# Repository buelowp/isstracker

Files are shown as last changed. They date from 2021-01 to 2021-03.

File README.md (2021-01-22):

# Use an opaque globe to show the position of the ISS using a laser
This project is going to project the ISS location on a globe showing current position continuously. The system uses a Particle Argon, one stepper motor for longitude rotation, and one servo motor for latitude rotation. It also uses a LOT of other parts listed in the BOM to make this work.

The goal is to provide a good looking device that is accurate and consistent. All of the motors and electronics must be hidden, and all parts must be independently moveable. So, the globe must be able to rotate without changing where the laser is pointing. The laser must work inside the globe independent of the base. The laser must also rotate 360 degrees longitude. The ISS does not go above or below ~60 degrees latitude, so a simple servo can be used for that.

A Particle project named isstracker

I found a similar project using an ESP8266 about 5 years ago and I was intrigued. So, I started hacking something up, but my requirements became much more complex than the original project. I wanted full rotation and to be able to *spin* the globe sitting on a base without changing where the location of the point showing the ISS.

It uses two independent sliprings which provide the ability to rotate the globe and the armature holding the laser without losing precision. It uses one 200 step NEMA stepper for longitude, and one 160 degree servo for the latitiude. The laser is from Sparkfun, but any laser that can be powered by 3 volts would work.

Pictures to follow

## Building it

Instructions to follow

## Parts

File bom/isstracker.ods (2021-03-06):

Part | Value | Device | Package | Description | MF | MPN | PROD_ID | VALUE
C1 | 100uF | 100UF-POLAR-RADIAL-2.5MM-25V-20% | CPOL-RADIAL-2.5MM-6.5MM | 100µF polarized capacitors |  |  | CAP-08439 | 100uF
C2 | 100uF | 100UF-POLAR-RADIAL-2.5MM-25V-20% | CPOL-RADIAL-2.5MM-6.5MM | 100µF polarized capacitors |  |  | CAP-08439 | 100uF
D1 | 1N4004 | 1N4004 | DO41-10 | DIODE | On Semi
H1 | MOUNT-HOLE3.0 | MOUNT-HOLE3.0 | 3,0 | MOUNTING HOLE with drill center marker
H2 | MOUNT-HOLE3.0 | MOUNT-HOLE3.0 | 3,0 | MOUNTING HOLE with drill center marker
H3 | MOUNT-HOLE3.0 | MOUNT-HOLE3.0 | 3,0 | MOUNTING HOLE with drill center marker
H4 | MOUNT-HOLE3.0 | MOUNT-HOLE3.0 | 3,0 | MOUNTING HOLE with drill center marker
H6 | MOUNT-HOLE2.8 | MOUNT-HOLE2.8 | 2,8 | MOUNTING HOLE with drill center marker
IC2 | L7805CV | MC7805CT-BPMS-ND | TO220V | Positive VOLTAGE REGULATOR
J1 | MOTOR_RIGHT | CONN_16 | 1X16 | Feather Header | Adafruit | 2886
J2 | MOTOR | CONN_04 | 1X04 | Multi connection point. Often used as Generic Header-pin footprint for 0.1 inch spaced/style header connections |  |  | CONN-09696
J3 | MOTOR_LEFT | CONN_12 | 1X12 | Feather Header
J4 | DISPLAY | CONN_07 | 1X07 | Multi connection point. Often used as Generic Header-pin footprint for 0.1 inch spaced/style header connections | Adafruit | 2886
J5 | GLOBE_RESET | CONN_02 | 1X02 | Multi connection point. Often used as Generic Header-pin footprint for 0.1 inch spaced/style header connections
J6 | CONTROL | CONN_04 | 1X04 | Multi connection point. Often used as Generic Header-pin footprint for 0.1 inch spaced/style header connections |  |  | CONN-09696
J8 | UART | CONN_03 | 1X03 | Multi connection point. Often used as Generic Header-pin footprint for 0.1 inch spaced/style header connections
J9 | DISTANCE | CONN_03 | 1X03 | Multi connection point. Often used as Generic Header-pin footprint for 0.1 inch spaced/style header connections
LED1 | LEDCHIPLED_1206 | XZDG55W-3 | CHIPLED_1206 | green smd LED | SunLED | XZDG55W-3
LED3 | LEDCHIPLED_1206 | XZDG55W-3 | CHIPLED_1206 | green smd LED | SunLED | XZDG55W-3
Q2 | IRL3103PBF | IRL3103PBF | TO220V | N-channel MOSFETs | Infineon | IRL3103PBF
R1 | 1k | RCG08051K00JNEA | 0805 | 1k smd resistor | Vishay Dale | RCG08051K00JNEA | RES-11622 | 1k
R2 | 1k | RCG08051K00JNEA | 0805 | 1k smd resistor | Vishay Dale | RCG08051K00JNEA | RES-08474 | 1k
R3 | 100 | CRCW0805100RJNEAC‎ | 0805 | 100 ohm smd resistor | Vishay Dale | CRCW0805100RJNEAC‎ | RES-08474 | 100
R4 | 10k | CRCW080510K0FKTA | 0805 | 10k smd resistor | Vishay Dale | CRCW080510K0FKTA | RES-08474 | 10k
R5 | 10k | CRCW080510K0FKTA | 0805 | 10k smd resistor | Vishay Dale | CRCW080510K0FKTA | RES-08474 | 10k
U1 | ARGON | ARGON | Feather | ARGON | Particle
X1 | +12V | KK-156-2 | KK-156-2 | KK 156 HEADER | MOLEX

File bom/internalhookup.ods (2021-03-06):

Part | Value | Device | Package | Description | AVAILABILITY | DESCRIPTION | MF | MP | PACKAGE | PRICE | PROD_ID | VALUE
C1 | 100uF | 100UF-POLAR-RADIAL-2.5MM-25V-20% | CPOL-RADIAL-2.5MM-6.5MM | 100µF polarized capacitors |  |  |  |  |  |  | CAP-08439 | 100uF
C3 | 100uF | 100UF-POLAR-RADIAL-2.5MM-25V-20% | CPOL-RADIAL-2.5MM-6.5MM | 100µF polarized capacitors |  |  |  |  |  |  | CAP-08439 | 100uF
CN1 | LASER | JST_2PIN-THM-RA | JST-PH-2-THM-RA | JST 2-Pin Connectors of various flavors
J2 | SERVO | CONN_03 | 1X03 | Multi connection point. Often used as Generic Header-pin footprint for 0.1 inch spaced/style header connections
J3 | CONTROL | CONN_04 | 1X04 | Multi connection point. Often used as Generic Header-pin footprint for 0.1 inch spaced/style header connections |  |  |  |  |  |  | CONN-09696
J4 | AZIMUTH | CONN_03 | 1X03 | Multi connection point. Often used as Generic Header-pin footprint for 0.1 inch spaced/style header connections
Q2 | SMMBT2222ALT | MMBT3904 | SOT95P240X120-3N | MMBT3904 Series 40 V CE Breakdown 0.2 A NPN General Purpose Amplifier - SOT-23 Check prices | Bad | Bipolar (BJT) Transistor NPN 40V 200mA 300MHz 300mW Surface Mount SOT-23-3 | STMicroelectronics | MMBT3904 | SOT-23-3 Taiwan Semiconductor | None
R1 | 1k | RCG08051K00JNEA | 0805 | 1k ohm resistor |  |  |  |  |  |  | RES-11622 | 0.3
U1 | AMS1117-3.3 | AMS1117-3.3 | SOT229P700X180-4N | Sot223/Pkg 1-Amp 3.3-Volt Low Drop Out Voltage Regulatator | Unavailable | Sot223/Pkg 1-Amp 3.3-Volt Low Drop Out Voltage Regulatator | Advanced Monolithic Systems | AMS1117-3.3 | SOT-89 ams | None

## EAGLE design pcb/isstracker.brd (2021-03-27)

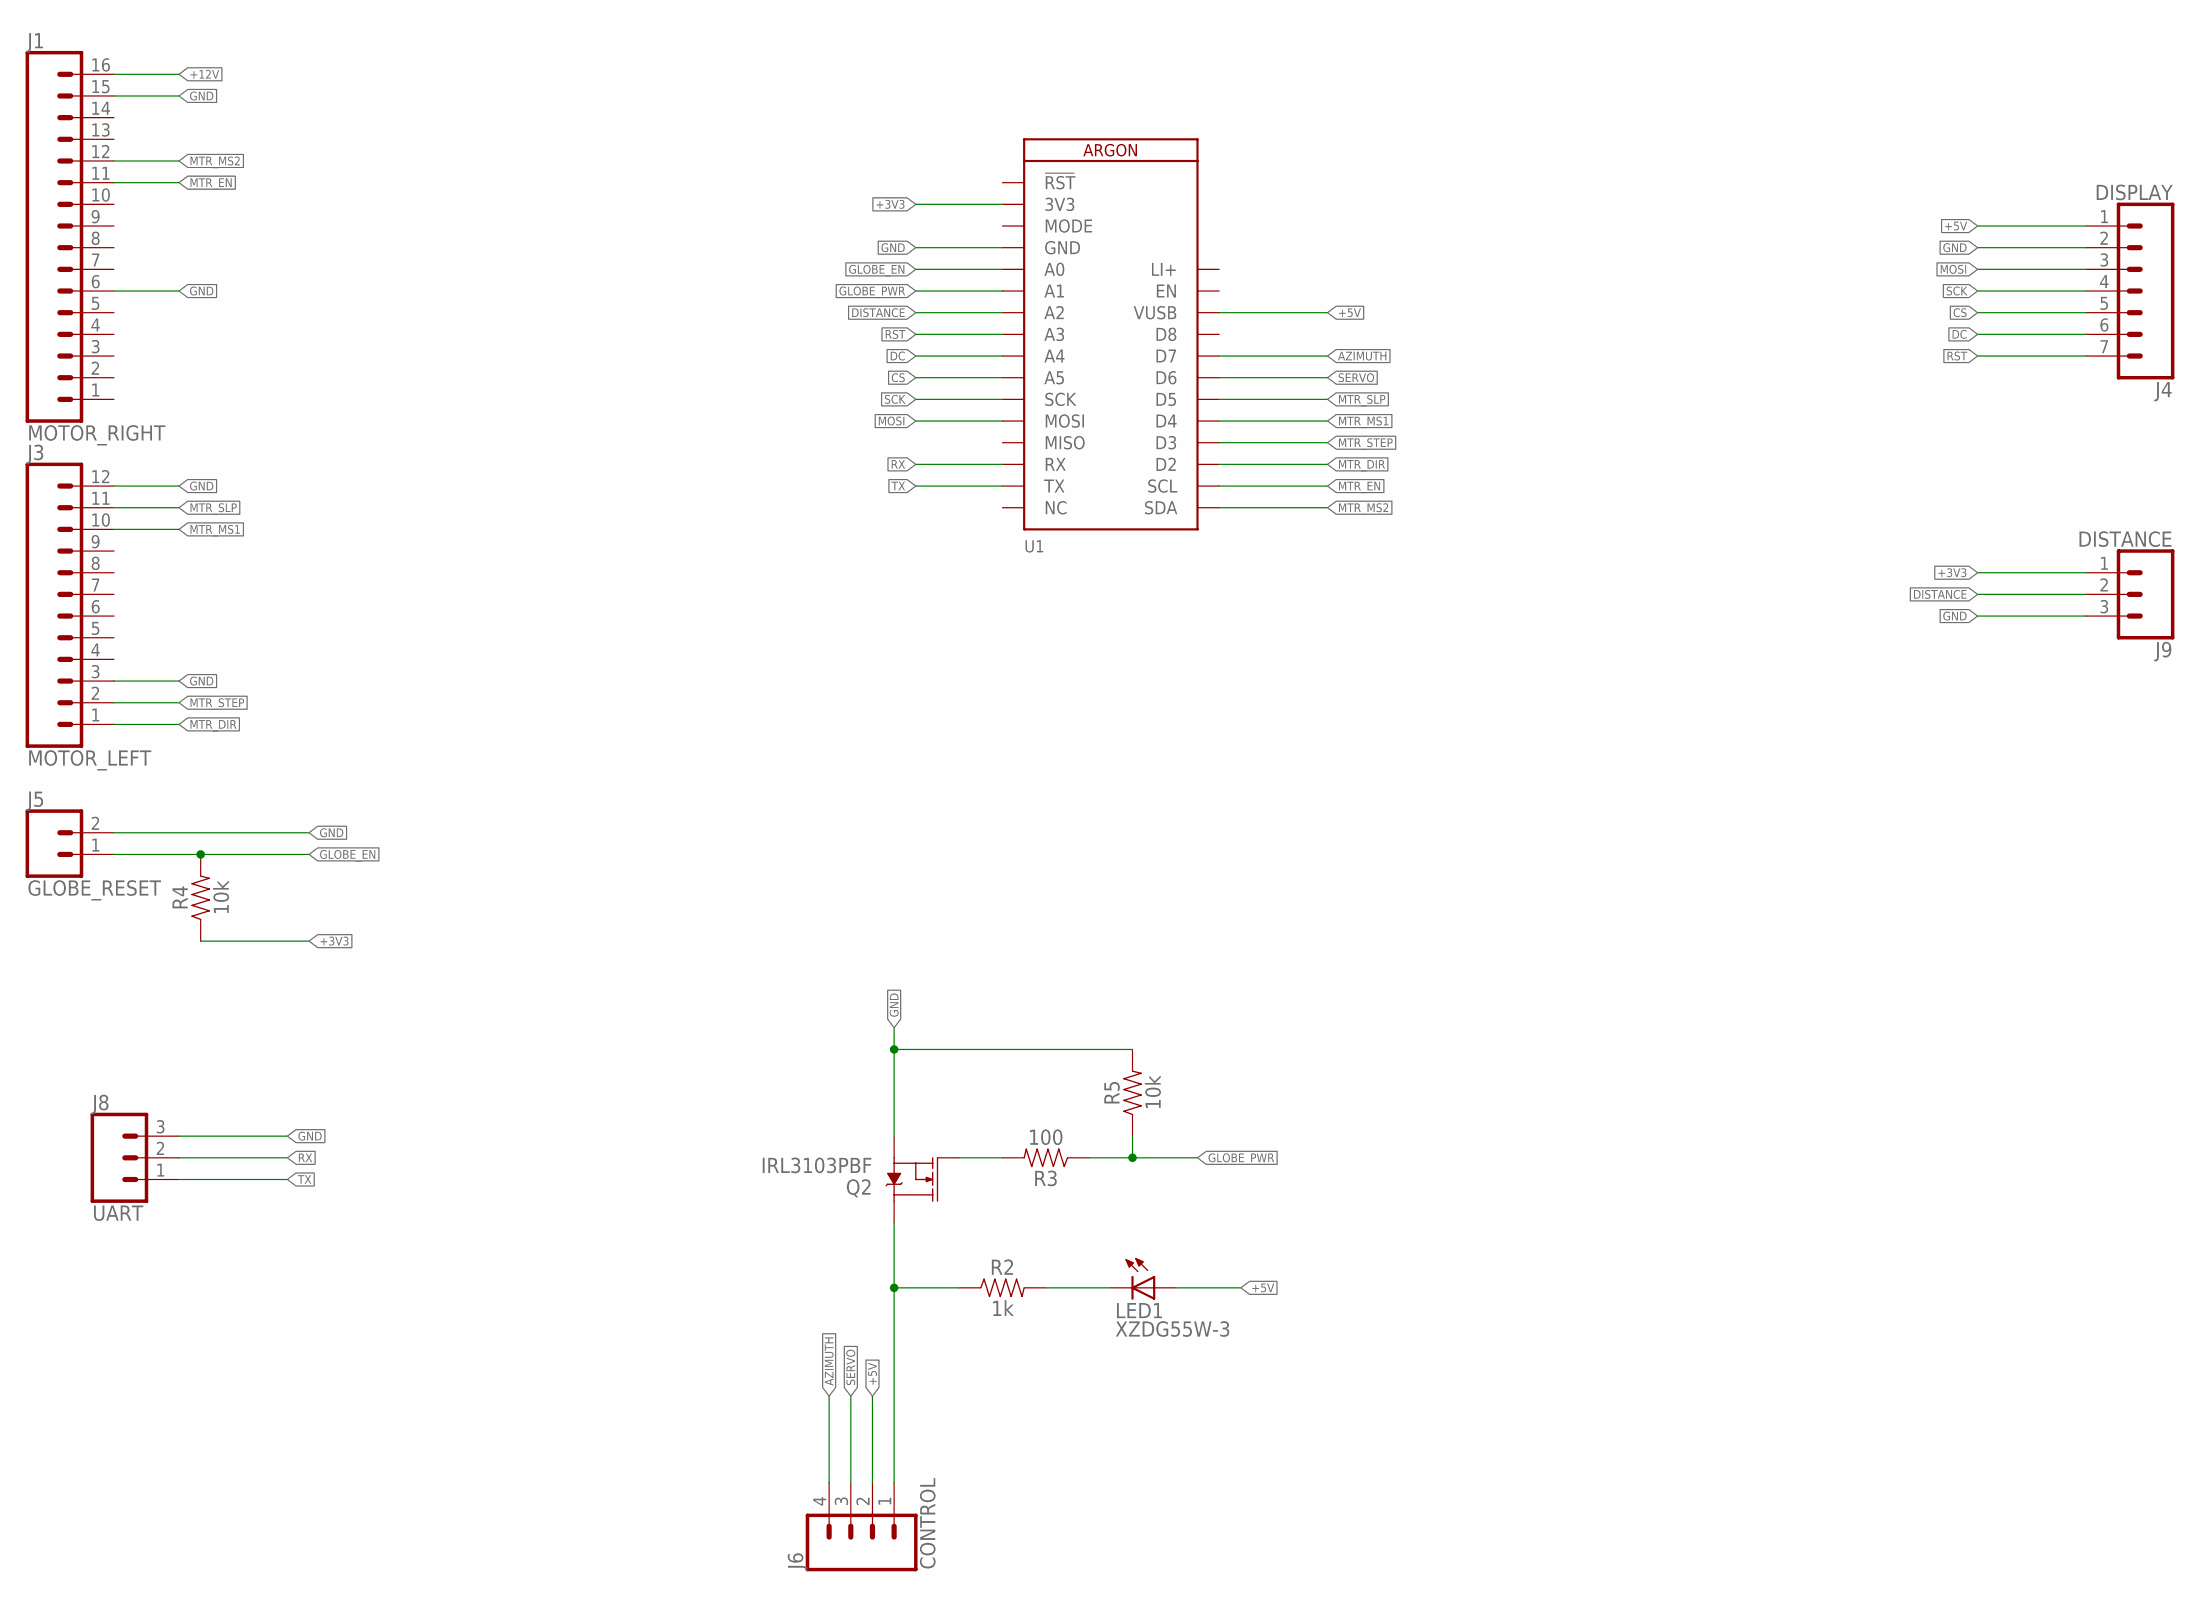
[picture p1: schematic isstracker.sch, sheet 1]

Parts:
J1: MOTOR_RIGHT; 1X16
J3: MOTOR_LEFT; 1X12
J4: DISPLAY; 1X07
J5: GLOBE_RESET; 1X02
J6: CONTROL; 1X04
J8: UART; 1X03
J9: DISTANCE; 1X03
LED1: XZDG55W-3; CHIPLED_1206
Q2: IRL3103PBF; TO220V
R2: 1k; 0805
R3: 100; 0805
R4, R5: 10k; 0805
U1: ARGON

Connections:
+3V3: J9.1, R4.1, U1.2 (3V3)
+5V: J4.1, J6.2, LED1.A, U1.26 (VUSB); also elsewhere on the board
+12V: J1.16; also elsewhere on the board
AZIMUTH: J6.4, U1.24 (D7)
CS: J4.5, U1.10 (A5)
DC: J4.6, U1.9 (A4)
DISTANCE: J9.2, U1.7 (A2)
GLOBE_EN: J5.1, R4.2, U1.5 (A0)
GLOBE_PWR: R3.1, R5.1, U1.6 (A1)
GND: J1.6, J1.15, J3.3, J3.12, J4.2, J5.2, J8.3, J9.3, Q2.3 (S), R5.2, U1.4 (GND); also elsewhere on the board
LI+: U1.28 (LI+)
MOSI: J4.3, U1.12 (MOSI)
MTR_DIR: J3.1, U1.19 (D2)
MTR_EN: J1.11, U1.18 (SCL)
MTR_MS1: J3.10, U1.21 (D4)
MTR_MS2: J1.12, U1.17 (SDA)
MTR_SLP: J3.11, U1.22 (D5)
MTR_STEP: J3.2, U1.20 (D3)
unnamed: Q2.1 (G), R3.2
unnamed: LED1.C, R2.2
unnamed: J6.1, Q2.2 (D), R2.1
RST: J4.7, U1.8 (A3)
RX: J8.2, U1.14 (RX)
SCK: J4.4, U1.11 (SCK)
SERVO: J6.3, U1.23 (D6)
TX: J8.1, U1.15 (TX)

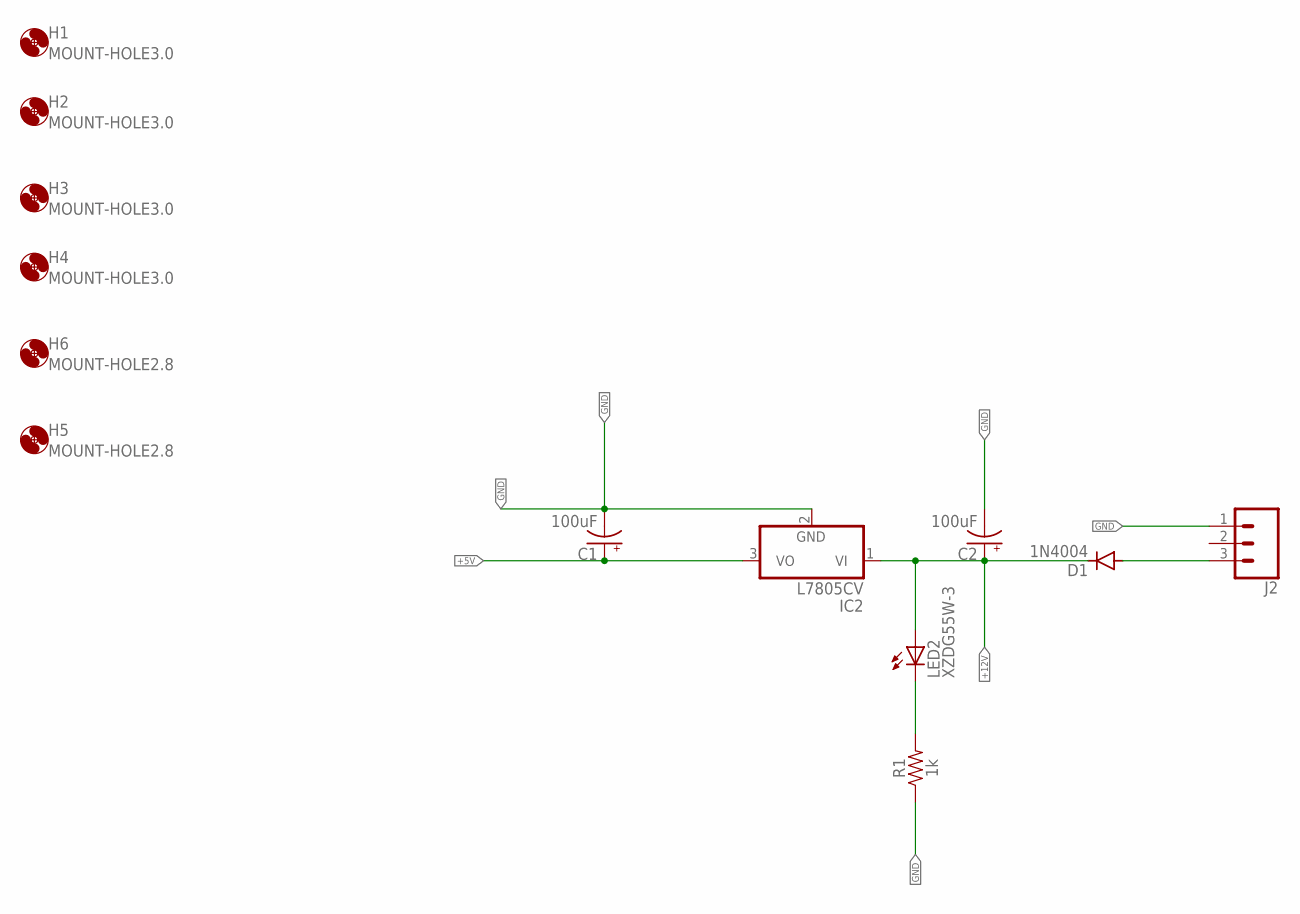
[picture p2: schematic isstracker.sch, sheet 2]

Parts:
C1, C2: 100uF; CPOL-RADIAL-2.5MM-6.5MM
D1: 1N4004; DO41-10
H1, H2, H3, H4: MOUNT-HOLE3.0; 3,0
H5, H6: MOUNT-HOLE2.8; 2,8
IC2: L7805CV; TO220V
J2: CONN_03LOCK_LONGPADS; 1X03_LOCK_LONGPADS
LED2: XZDG55W-3; CHIPLED_1206
R1: 1k; 0805

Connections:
+5V: C1.1 (+), IC2.3 (VO); also elsewhere on the board
+12V: C2.1 (+), D1.C, IC2.1 (VI), LED2.A; also elsewhere on the board
GND: C1.2 (-), C2.2 (-), IC2.2 (GND), J2.1, R1.1; also elsewhere on the board
unnamed: D1.A, J2.3
unnamed: LED2.C, R1.2

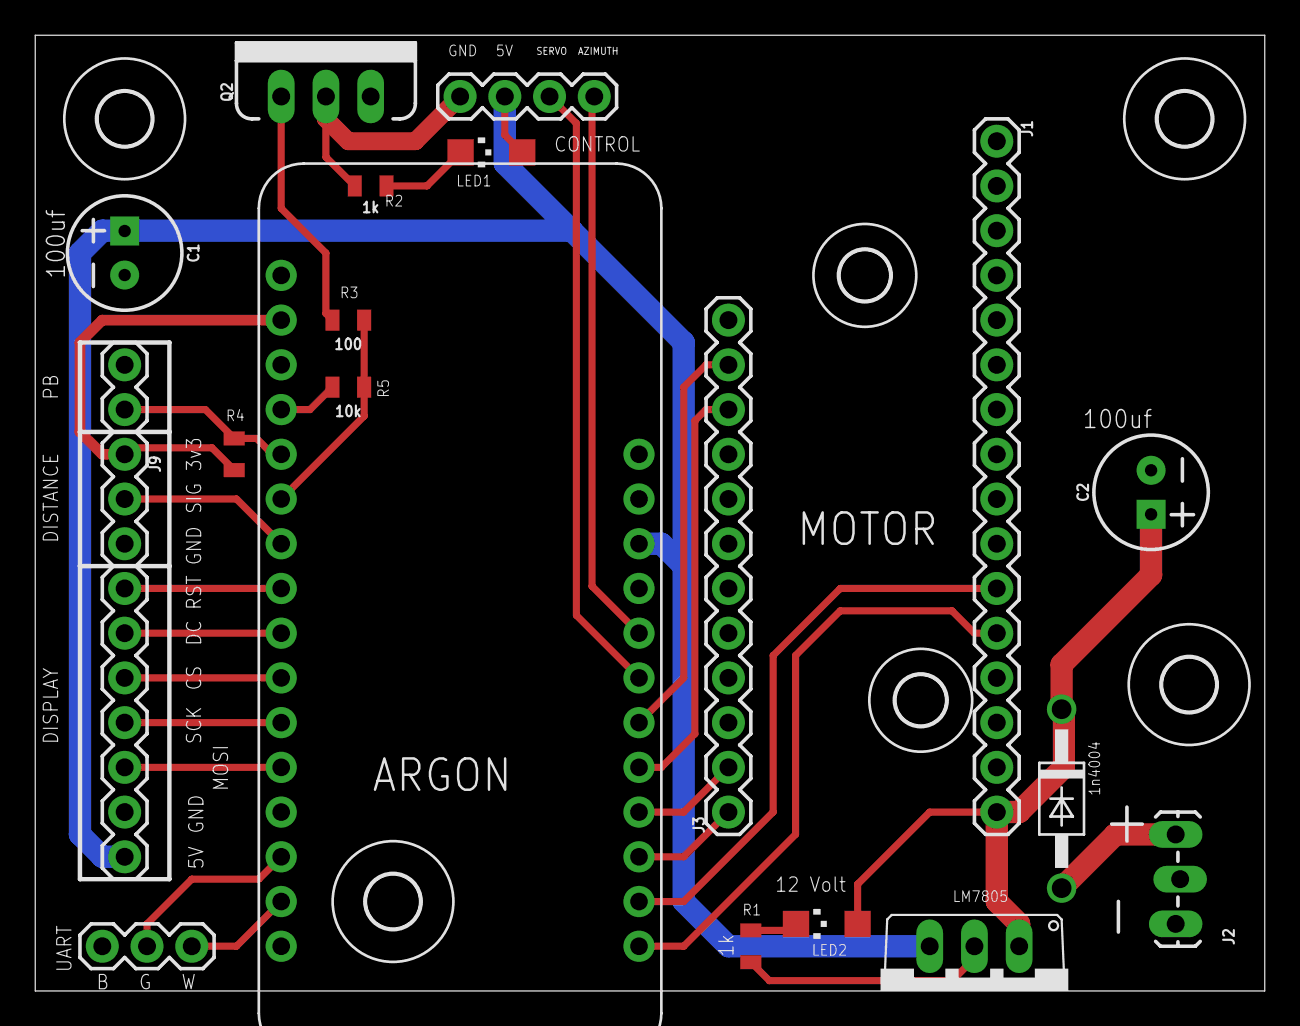
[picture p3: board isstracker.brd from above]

Board: 2 copper layers, 69.8 x 54.3 mm, 27 parts (0 on the bottom side), 27 nets.

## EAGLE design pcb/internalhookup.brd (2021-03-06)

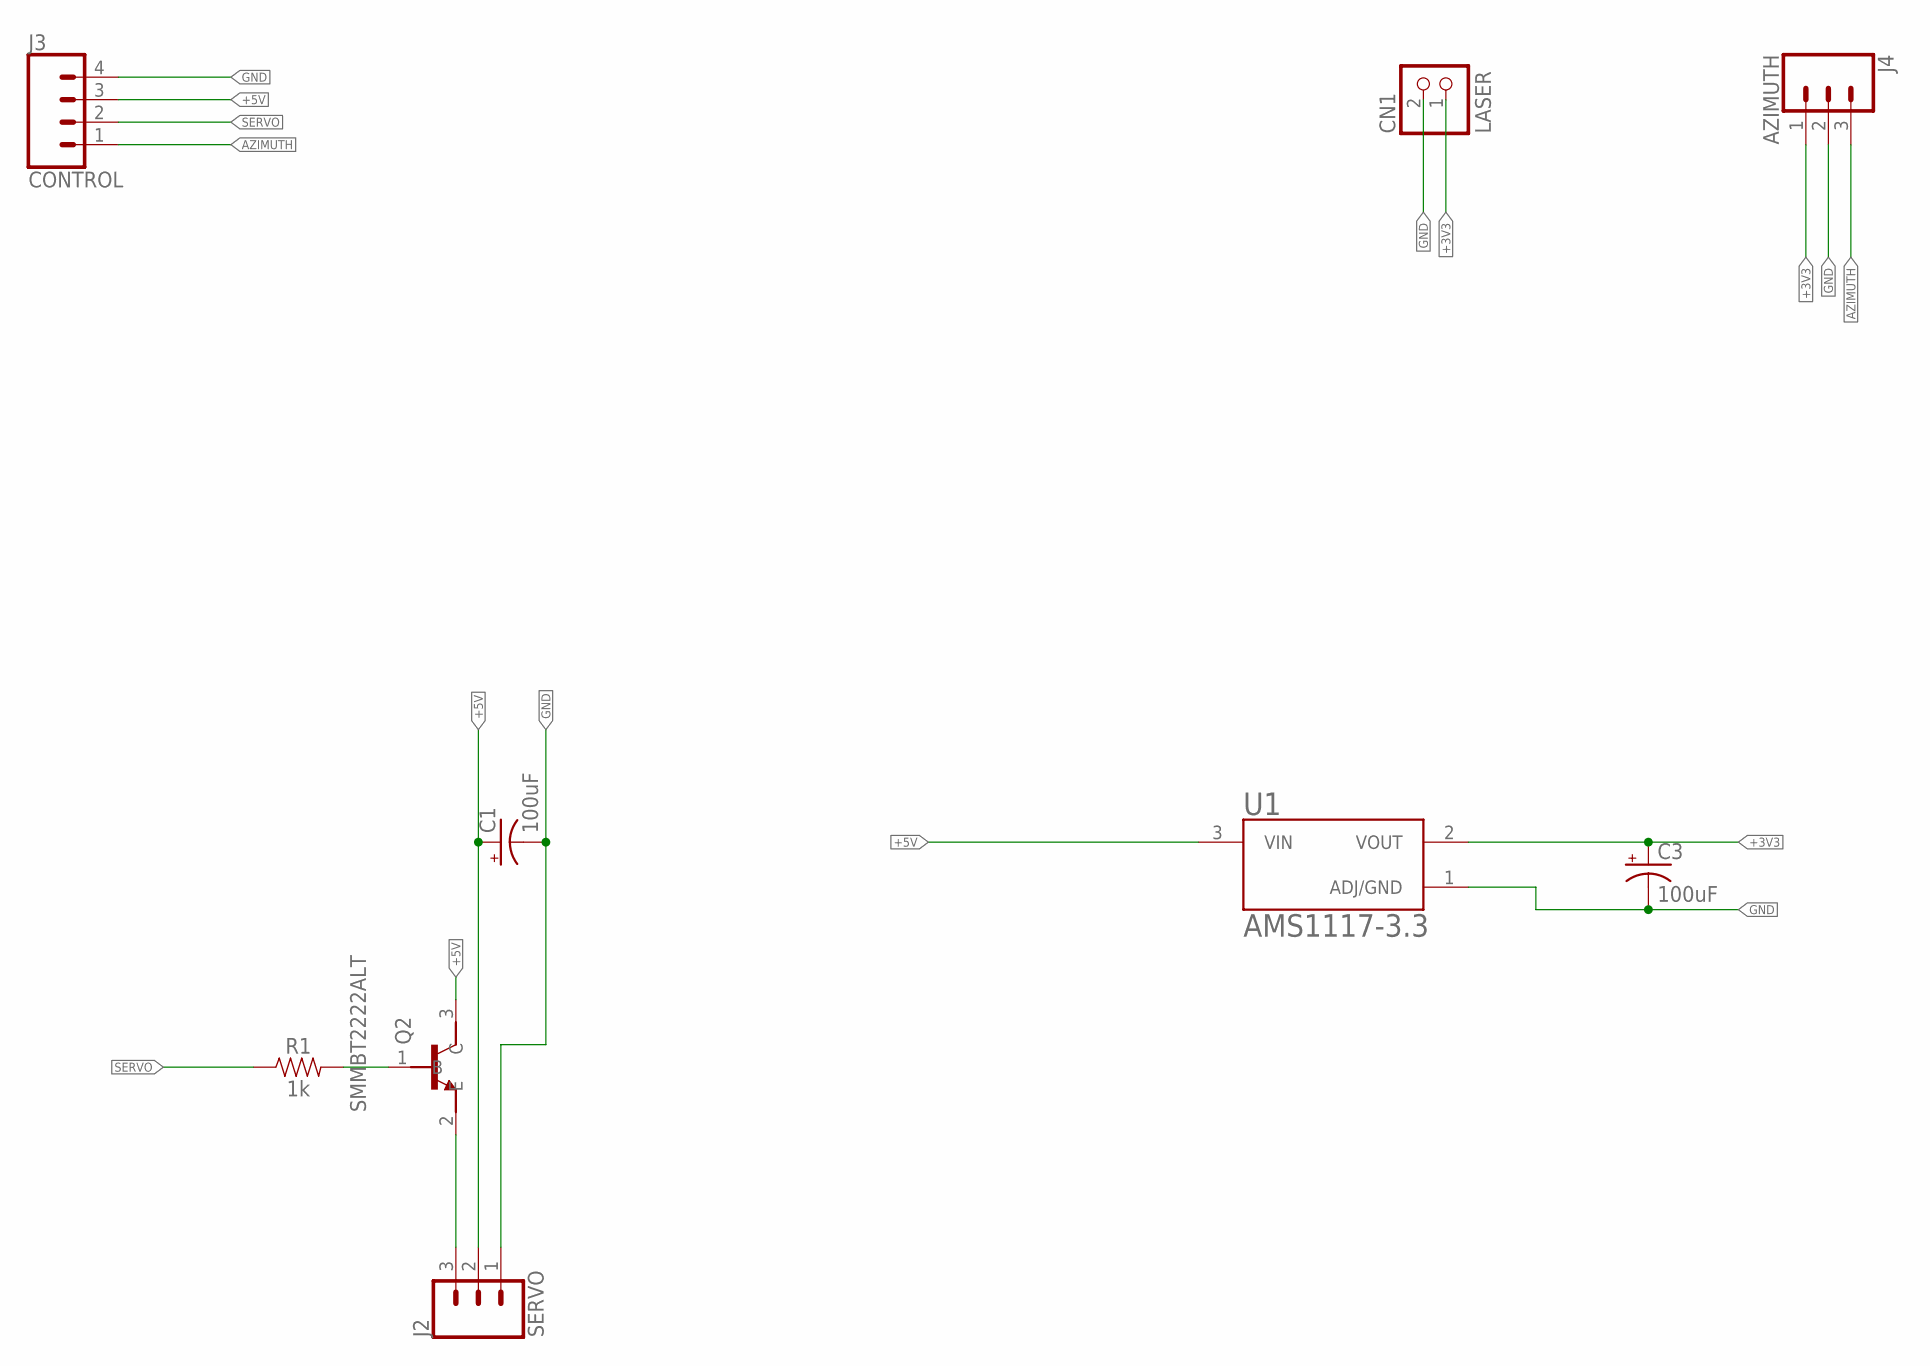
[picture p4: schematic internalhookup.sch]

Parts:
C1, C3: 100uF; CPOL-RADIAL-2.5MM-6.5MM
CN1: LASER; JST-PH-2-THM-RA
J2: SERVO; 1X03
J3: CONTROL; 1X04
J4: AZIMUTH; 1X03
Q2: SMMBT2222ALT; SOT95P240X120-3N
R1: 1k; 0805
U1: AMS1117-3.3; SOT229P700X180-4N

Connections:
+3V3: C3.1 (+), CN1.1 (2), J4.1, U1.2 (VOUT)
+5V: C1.1 (+), J2.2, J3.3, Q2.3 (C), U1.3 (VIN)
AZIMUTH: J3.1, J4.3
GND: C1.2 (-), C3.2 (-), CN1.2 (1), J2.1, J3.4, J4.2, U1.1 (ADJ/GND)
unnamed: Q2.1 (B), R1.2
unnamed: J2.3, Q2.2 (E)
SERVO: J3.2, R1.1

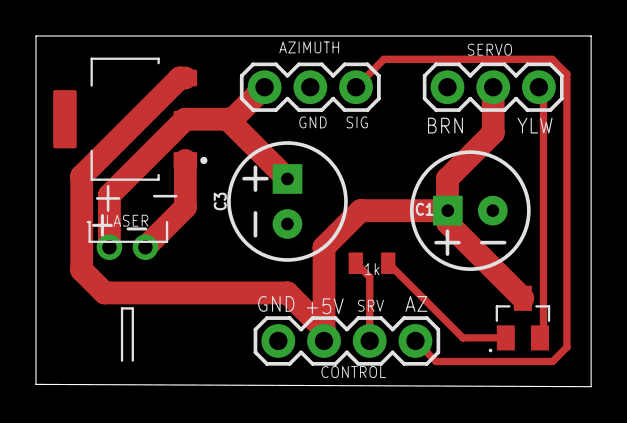
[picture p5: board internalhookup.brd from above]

Board: 2 copper layers, 30.8 x 19.5 mm, 9 parts (0 on the bottom side), 7 nets.

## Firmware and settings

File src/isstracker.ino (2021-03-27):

#include "Adafruit_mfGFX.h"
#include "Adafruit_SSD1351_Photon.h"

#define APP_ID              57
#define BOARD_REV_1_6       1

#define miso                A7      // used by library internally, defined here to avoid confusion
#define mosi                A6      // used by library internally, defined here to avoid confusion
#define cs                  A5
#define rst                 A3
#define dc                  A4
#define DISTANCE            A2
#define GLOBE_POWER         A1
#define GLOBE_EN            A0

#define mtr_ms2             D0
#define mtr_en              D1
#define mtr_dir             D2
#define mtr_step            D3
#define mtr_ms1             D4
#define mtr_slp             D5
#define SERVO               D6
#define AZIMUTH             D7

#define FULL_STEP           1
#define HALF_STEP           2
#define QUARTER_STEP        3
#define EIGHTH_STEP         4

#define CLOCKWISE           1
#define CCLOCKWISE          2

#define INC_CAL_ADDRESS     0

// system_tick_t values as it's measured in millis
#define ONE_SECOND          1000
#define FIVE_SECONDS        (ONE_SECOND * 5)
#define TEN_SECONDS         (ONE_SECOND * 10)
#define TWENTY_SECONDS      (ONE_SECOND * 20)
#define ONE_MINUTE          (ONE_SECOND * 60)
#define FIVE_MINUTES        (ONE_MINUTE * 5)
#define TEN_MINUTES         (ONE_MINUTE * 10)
#define THIRTY_MINUTES      (ONE_MINUTE * 30)
#define ONE_HOUR            (ONE_MINUTE * 60)
#define TWO_HOURS           (ONE_HOUR * 2)

#define ISS_BLACK           0x0000
#define ISS_BLUE            0x001F
#define ISS_RED             0xF800
#define ISS_GREEN           0x07E0
#define ISS_CYAN            0x07FF
#define ISS_MAGENTA         0xF81F
#define ISS_YELLOW          0xFFE0  
#define ISS_WHITE           0xFFFF

Timer issUpdate(5000, run_location_update);
SerialLogHandler logHandler;
Serial1LogHandler logHandler2(115200);

Servo servo;
double g_longitude;
double g_latitude;
int g_lon;
int g_lat;
int g_appId;
int g_azimuthPosition;
int g_incOffset;
int g_currentResolution;
int g_motorAngle;
int g_servoAngle;
int g_motorDirection;
int g_lastResetReason;
int g_displayTimeout;
int g_globeTimeout;
int g_distance;
int g_proximity;
system_tick_t g_displayTimeoutMillis;
system_tick_t g_globeTimeoutMillis;
bool g_querySuccess;
bool g_runLocationQuery;
bool g_inCalibration;
bool g_motorDecCalibrated;
bool g_motorHome;
bool g_motorEnabled;
bool g_inclineHome;
bool g_displayEnabled;
bool g_cycleColors;
bool g_globeEnabled;
bool g_globePowerControl;
String g_version = System.version() + "." + APP_ID;

Adafruit_SSD1351 display = Adafruit_SSD1351(cs, dc, rst);

void set_motor_sleep(bool slp)
{
    if (slp) {
        Log.info("%s: Putting motor to sleep", __FUNCTION__);
        digitalWrite(mtr_slp, LOW);
        delay(250);
    }
    else {
        Log.info("%s: Waking motor up", __FUNCTION__);
        digitalWrite(mtr_slp, HIGH);
        delay(250);
    }
}

void set_motor_home()
{
    set_motor_step_resolution(FULL_STEP);
    set_motor_enabled(true);
    set_motor_sleep(false);

    // If we seem like we are home, make a
    // quarter turn so we can rotate and hit
    // the leading edge of the sensor to be consistent
    Log.info("%s: Moving motor away from sensor...", __FUNCTION__);
    set_motor_dir(CLOCKWISE);
    if (digitalRead(AZIMUTH) == LOW) {
        for (int i = 0; i < 50; i++) {
            digitalWrite(mtr_step, HIGH);
            delay(1);
            digitalWrite(mtr_step, LOW);
            delay(1);
        }
    }

    // This will be slow!
    Log.info("%s: Moving motor back to home!", __FUNCTION__);
    set_motor_dir(CCLOCKWISE);
    for (int i = 0; i < 200; i++) {
        digitalWrite(mtr_step, HIGH);
        delay(1);
        digitalWrite(mtr_step, LOW);
        delay(200);
        if (digitalRead(AZIMUTH) == LOW) {
            break;
        }
        Particle.process();
    }
    set_motor_sleep(true);
    g_azimuthPosition = 0;
    g_motorHome = true;
}

void reset_motor()
{
    set_motor_sleep(false);
    set_motor_enabled(true);
    set_motor_dir(CLOCKWISE);
    set_motor_step_resolution(FULL_STEP);
    set_motor_home();
    set_motor_sleep(true);
    Log.info("%s: motor reset complete", __FUNCTION__);
}

void set_motor_dir(int dir)
{
    switch (dir) {
        case CCLOCKWISE:
            digitalWrite(mtr_dir, HIGH);
            g_motorDirection = CCLOCKWISE;
            Log.info("%s: Set motor direction to clockwise", __FUNCTION__);
            break;
        case CLOCKWISE:
        default:
            digitalWrite(mtr_dir, LOW);
            g_motorDirection = CLOCKWISE;
            Log.info("%s: Set motor direction to counter clockwise", __FUNCTION__);
            break;
    }
}

void set_motor_step_resolution(int step)
{
    switch (step) {
        case HALF_STEP:
            digitalWrite(mtr_ms1, HIGH);
            digitalWrite(mtr_ms2, LOW);
            g_currentResolution = 400;
            Log.info("%s: Set stepper resolution to half steps (400)", __FUNCTION__);
            break;
        case QUARTER_STEP:
            digitalWrite(mtr_ms1, LOW);
            digitalWrite(mtr_ms2, HIGH);
            g_currentResolution = 800;
            Log.info("%s: Set stepper resolution to quarter steps (800)", __FUNCTION__);
            break;
        case EIGHTH_STEP:
            digitalWrite(mtr_ms1, HIGH);
            digitalWrite(mtr_ms2, HIGH);
            g_currentResolution = 1600;
            Log.info("%s: Set stepper resolution to eighth steps (1600)", __FUNCTION__);
            break;
        case FULL_STEP:
        default:
            digitalWrite(mtr_ms1, LOW);
            digitalWrite(mtr_ms2, LOW);
            g_currentResolution = 200;
            Log.info("%s: Set stepper resolution to single steps (200)", __FUNCTION__);
            break;
    }
}

/**
 * \fn void set_motor_enabled(bool en)
 * \param en Flag for motor state
 * 
 * Set to true, and drive pin LOW to enable the easy driver, false
 * drives the pin HIGH which disables the driver.
 */
void set_motor_enabled(bool en)
{
    if (en) {
        digitalWrite(mtr_en, LOW);
        g_motorEnabled = true;
        Log.info("%s: motor is enabled", __FUNCTION__);
    }
    else {
        digitalWrite(mtr_en, HIGH);
        g_motorEnabled = false;
        Log.info("%s: motor is disabled", __FUNCTION__);
    }
}
 
 /**
  * When we need to move the motor, turn the outputs
  * on which is what SLP going HIGH does. This should
  * help keep the motor cooler during operation.
  */
void set_motor_position(int angle)
{
    g_motorAngle = angle;

    if ((g_azimuthPosition == g_currentResolution - 1) && angle >= 0) {
        g_azimuthPosition = -1;
    }
    int steps = angle - g_azimuthPosition;
    if (steps > 0) {
        set_motor_sleep(false);
        Log.info("%s: Moving motor %d steps", __FUNCTION__, steps);
        g_motorHome = false;
    }
    for (int i = 0; i < steps; i++) {
        digitalWrite(mtr_step, HIGH); //Trigger one step forward
        delay(1);
        digitalWrite(mtr_step, LOW); //Pull step pin low so it can be triggered again
        delay(1);
        g_azimuthPosition++;
    }

    if (steps > 0)
        set_motor_sleep(true);
}

/**
 * \fn void iss_location(const char *event, const char *data) 
 * \param event Pointer to the event name returned by the webhook
 * \param data The actual JSON data returned by the webhook
 * 
 * This is a Particle webhook return function which translates
 * the JSON from the API into a latitude and longitude the
 * control board can understand and move towards.
 */
void iss_location(const char *event, const char *data) 
{
    JSONValue outerObj = JSONValue::parseCopy(data);

    g_querySuccess = false;

    JSONObjectIterator iter(outerObj);
    while (iter.next()) {
        if (iter.value().isObject()) {
            JSONObjectIterator location(iter.value());
            while (location.next()) {
                if (location.name() == "longitude") {
                    g_longitude = location.value().toDouble();
                    g_lon = 180 - g_longitude;
                }
                if (location.name() == "latitude") {
                    g_latitude = location.value().toDouble();
                    set_servo_angle();
                }
            }
        }
        else {
            if (iter.name() == "message") {
                if (iter.value().toString() == "success") {
                    g_querySuccess = true;
                }
            }
        }
    }

    if (g_querySuccess) {
        set_inclination();
        set_declination();
        Log.info("%s: %f, %f, inclination %d, azimuth %d, motor position %d", __FUNCTION__, g_latitude, g_longitude, g_servoAngle, g_motorAngle, g_azimuthPosition);
    }
    else {
        Log.info("JSON did not work right");
    }
}

/**
 * \fn int set_servo_angle()
 * 
 * We need to do a bit of math to translate the latitude
 * into servo angles. That's done here. We round up so we're
 * only moving when the angle is greater than x.5 which means
 * it should always be at the actual angle.
 */
int set_servo_angle()
{
    int angle = static_cast<int>(g_latitude + .5);
    angle += 90;
    angle += g_incOffset;
    g_servoAngle = angle;
    Log.info("%s: Angle set to %d", __FUNCTION__, angle);
    return angle;
}

/**
 * \fn void run_location_update()
 * 
 * Tell the location function to run, as we only do it
 * every 5 or so seconds and we don't want to do it
 * in a timer ISR which would crash the system. Basically
 * this is a poor semaphore.
 */
void run_location_update()
{
    if (!g_inCalibration)
        g_runLocationQuery = true;
}

/**
 * \fn void set_inclination(int angle)
 * \param angle The Angle we are telling the servo to rotate to
 * 
 * Sets laser position in absolute angle (it's a servo)
 * So we an just ignore this if the globe power is off, as
 * the next time it's called, the servo will just go where
 * the angle tells it to, no history needed.
 * This function sets the angle directly.
 */
void set_inclination(int angle)
{
    if (!g_globeEnabled)
        return;

    if (angle > 20 && angle < 160) {
        servo.write(angle);
        g_servoAngle = angle;
    }
    if (g_servoAngle == 90)
        g_inclineHome = true;
    
    Log.info("%s: Inclination set to %d", __FUNCTION__, g_servoAngle);
}

/**
 * \fn void set_inclination()
 * 
 * Sets laser position in absolute angle (it's a servo)
 * So we an just ignore this if the globe power is off, as
 * the next time it's called, the servo will just go where
 * the angle tells it to, no history needed.
 * This function assumes the angle is already calculated.
 */
void set_inclination()
{
    static int lastAngle = 200;

    if (!g_globeEnabled)
        return;

    if (g_inCalibration)
        return;

    if (lastAngle != g_servoAngle) {
        servo.write(g_servoAngle);

        lastAngle = g_servoAngle;
    }
    Log.info("%s: Inclination set to %d", __FUNCTION__, g_servoAngle);
}

/**
 * \fn void set_declination()
 * 
 * Translate the longitude into a value we can set the
 * stepper motor to.
 */
void set_declination()
{  
    int angle = 0;
    int degrees = 0;

    if (g_inCalibration)
        return;

    degrees = static_cast<int>(g_longitude * 10);
    angle = map(degrees, 0, 3600, 0, g_currentResolution);

    if (angle < 0)
        angle = g_currentResolution + angle;

    set_motor_position(angle);
}

/**
 * \fn int web_calibrate(String p)
 * \param p String from Particle web
 * \return Returns the int representation of the string sent
 * 
 * This will enable a calibration state so we can change the
 * lat and lon angles if necessary without removing the globe.
 * To do this, we assume the globe needs to be turned back on
 * so calibration doesn't fail in the middle if globe power turns
 * off.
 */
int web_calibrate(String p)
{    
    if (p.toInt() != 0) {
        g_globeTimeoutMillis = millis() + ONE_HOUR;
        g_globeEnabled = true;
        set_motor_enabled(true);
        
        g_inCalibration = true;
        Log.info("%s: starting calibration", __FUNCTION__);
    }
    else {
        g_inCalibration = false;
        Log.info("%s: ending calibration", __FUNCTION__);
    }

    return p.toInt();
}

int web_rotate_clockwise(String p)
{
    int steps = p.toInt();
    steps *= g_currentResolution;

    if (!g_inCalibration)
        return -1;

    if (steps >= 0 && steps < 360) {
        Log.info("%s: Moving azimuth motor %d steps clockwise", __FUNCTION__, steps);
        set_motor_dir(CLOCKWISE);
        set_motor_position(steps);
        return steps;
    }

    return 0;
}

int web_rotate_cclockwise(String p)
{
    int steps = p.toInt();
    steps *= g_currentResolution;

    if (!g_inCalibration)
        return -1;

    if (steps > 0 && steps < 180) {
        Log.info("%s: Moving azimuth motor %d steps counter clockwise", __FUNCTION__, steps);
        set_motor_dir(CCLOCKWISE);
        set_motor_position(steps);
        return steps;
    }

    return 0;
}

int web_set_motor_resolution(String p)
{
    int res = p.toInt();

    set_motor_step_resolution(res);
    return g_currentResolution;
}

int web_jog_inclination(String p)
{
    int jog = p.toInt();

    if (g_inCalibration && g_inclineHome) {
        if (jog > 0) {
            g_servoAngle++;
            servo.write(g_servoAngle);
            g_incOffset++;
        }
        if (jog < 0) {
            g_servoAngle--;
            servo.write(g_servoAngle);
            g_incOffset--;
        }
        EEPROM.put(INC_CAL_ADDRESS, g_incOffset);
    }

    Log.info("%s: Inclination offset is now %d", __FUNCTION__, g_incOffset);
    return g_incOffset;
}

int web_set_incline_offset(String p)
{
    int offset = p.toInt();

    if (offset > -11 && offset < 11) {
        g_incOffset = offset;
        EEPROM.put(INC_CAL_ADDRESS, offset);
    }

    Log.info("%s: Inclination offset set to %d", __FUNCTION__, g_incOffset);
    return offset;
}

int web_set_display_timeout(String p)
{
    int timeout = p.toInt() * 1000;

    if (timeout >= TEN_SECONDS && timeout <= TEN_MINUTES) {
        g_displayTimeout = timeout;
        return timeout;
    }
    return g_displayTimeout;
}

void display_update()
{
    if (!g_displayEnabled) {
        return;
    }

    display.setCursor(0,0);
    display.setTextSize(1);
    display.setTextColor(ISS_WHITE, ISS_BLACK);
    display.printf("Version: %s\n\n", g_version.c_str());
    display.setTextColor(ISS_CYAN, ISS_BLACK);
    display.printf("ISS Location\n\n");
    if (g_latitude < 0) {
        display.setTextColor(ISS_BLUE, ISS_BLACK);
        display.printf("Lat: %10.06f S  \n", g_latitude);
    }
    else {
        display.setTextColor(ISS_GREEN, ISS_BLACK);
        display.printf("Lat: %10.06f N \n", g_latitude);
    }
    if (g_longitude < 0) {
        display.setTextColor(ISS_BLUE, ISS_BLACK);
        display.printf("Lon: %10.06f W \n", g_longitude);
    }
    else {
        display.setTextColor(ISS_GREEN, ISS_BLACK);
        display.printf("Lon: %10.06f E \n", g_longitude);
    }
    display.setTextColor(ISS_WHITE, ISS_BLACK);
    display.printf("\n\nLaser State: ");
    if (g_globeEnabled) {
        display.setTextColor(ISS_GREEN, ISS_BLACK);
        display.printf("ON");
    }
    else {
        display.setTextColor(ISS_RED, ISS_BLACK);
        display.printf("OFF");
    }
//    Log.info("%s: Lat: %f, Lon: %f", __FUNCTION__, g_latitude, g_longitude);
}

bool detect_motion()
{
    if (digitalRead(DISTANCE) == HIGH) {
        if (g_displayTimeoutMillis < millis()) {
            g_displayEnabled = true;
            g_displayTimeoutMillis = millis() + g_displayTimeout;
            return true;
        }
    }
    else {
        if (g_displayTimeoutMillis < millis()) {
            g_displayEnabled = false;
            display.fillScreen(0);
        }
    }
    return false;
}

int web_set_proximity_distance(String p)
{
    int distance = p.toInt();
    if (distance > 12 && distance < 150) {
        g_proximity = distance;
    }
    return g_proximity;
}

int web_enable_globe(String p)
{
    int enable = p.toInt();

    if (enable == 0) {
        g_globeEnabled = false;
        g_globeTimeoutMillis = 0;
        digitalWrite(GLOBE_POWER, LOW);
        return 0;
    }
    g_globeTimeoutMillis = millis() + ONE_HOUR;
    g_globeEnabled = true;
    digitalWrite(GLOBE_POWER, HIGH);
    return 1;
}

void check_globe_state()
{
    if (millis() <= g_globeTimeoutMillis) {
        return;
    }
    else {
        if (digitalRead(GLOBE_EN) == LOW) {
            g_globeTimeoutMillis = millis() + ONE_HOUR;
            g_globeEnabled = true;
            return;
        }
    }
    if (g_globeEnabled) {
        digitalWrite(GLOBE_POWER, LOW);
        g_globeEnabled = false;
    }
}

void print_reset_reason()
{
    switch (System.resetReason()) {
        case RESET_REASON_UNKNOWN:
            Log.info("setup: Last Reset: Unknown reset!");
            display.println("Unknown reset!");
            break;
        case RESET_REASON_PIN_RESET:
            Log.info("setup: Last Reset: Reset due to reset button press!");
            display.println("Pushbutton reset!");
            break;
        case RESET_REASON_POWER_MANAGEMENT:
            Log.info("setup: Last Reset: Reset due to power management!");
            display.println("Reset due to PM!");
            break;
        case RESET_REASON_WATCHDOG:
            Log.info("setup: Last Reset: Watchdog reset!");
            display.println("Watchdog reset!");
            break;
        case RESET_REASON_UPDATE:
            Log.info("setup: Last Reset: Update finished!");
            display.println("Update finished!");
            break;
        case RESET_REASON_UPDATE_ERROR:
            Log.info("setup: Last Reset: Update failed!");
            display.println("Update failed!");
            break;
        case RESET_REASON_UPDATE_TIMEOUT:
            Log.info("setup: Last Reset: Update timed out!");
            display.println("Update timed out!");
            break;
        case RESET_REASON_FACTORY_RESET:
            Log.info("setup: Last Reset: Factory reset performed!");
            display.println("actory reset");
            break;
        case RESET_REASON_SAFE_MODE:
            Log.info("setup: Last Reset: Reset into safe mode!");
            display.println("Safe mode!");
            break;
        case RESET_REASON_DFU_MODE:
            Log.info("setup: Last Reset: Reset from DFU!");
            display.println("DFU!");
            break;
        case RESET_REASON_PANIC:
            Log.info("setup: Last Reset: System panic!");
            display.println("System panic!");
            break;
        case RESET_REASON_USER:
            Log.info("setup: Last Reset: User code called for a reset!");
            display.println("User reset!");
            break;
        default:
        case RESET_REASON_NONE:
            Log.info("setup: No reset reason given, resetReason returned %d!", System.resetReason());
            display.println("Unknown");
            break;
    }
}
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
void loop() 
{
    static int lastHour = 24;

    if (g_runLocationQuery) {
        Particle.publish("iss_location", PRIVATE);
        g_runLocationQuery = false;
    }

    if (Time.hour() != lastHour) {
        Particle.syncTime();
        waitUntil(Particle.syncTimeDone);
        lastHour = Time.hour();
    }
    if (g_inCalibration) {
        if (!g_motorHome)
            set_motor_home();

        if (!g_inclineHome)
            set_inclination(90);
    }
    detect_motion();
    display_update();
    check_globe_state();
}

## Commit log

2020-05-09 Fixed a bug with latitude calculations
    [isstracker.ino]
2020-05-09 Fixes
    * Fixed a rounding problem
    * Changed a variable name to be more explicit
    [isstracker.ino]
2021-01-22 Tracker version 45:
    * Cleaning up prints to the display
    * Migrating back to the git src, it's been on it's own for a while
2021-01-22 Updating repo with the non source code portions
    [internalhookup.brd, internalhookup.sch, isstracker.brd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]
2021-01-22 Fixing PCB to use the new IR sensor instead.
    [isstracker.brd, isstracker.sch]
2021-01-24 Version 47:
    * Only wake motor from sleep IFF we are going to move the motor
    * Clean up some extra logging
    * Add LED controls for the globe lighting
    * This includes the first PCB sent out for production at OSHPark
    [internalhookup.brd, isstracker.brd, isstracker.sch]
2021-02-06 Version 48
    * Added some colors and made it possible to cycle them on a timer
    * Fixed a display bug
    [isstracker.ino]
2021-02-07 Updating to the latest PCB to fix breaking issues
    * Fixed capacitor sets for both boards to be larger and polarized on the
    LDO's
    * Fixed left track for motor board as it was 1 pin too short
    * Switched from Declination to Azimuth
    * Moved Azimuth signaling to the internal board to allow for movement
    * Removed resistors on 5V LED signal buffer
    * Switch LED pinout to match the Lumenati ordering
    * Internal board got a polarized capacitor
    * Internal board layout moved around to better match reality
    [internalhookup.brd, internalhookup.sch, isstracker.brd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]
2021-02-08 Adding laser control
    * Hookup an NPN to be able to turn the laser on/off via A0
    [internalhookup.brd, internalhookup.sch, isstracker.brd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]
2021-02-09 Adding a duty cycle switch for a Laser
    * Currently unused, the laser I chose does it's own duty cycle, but
    for lasers that can't be on all the time, this will help.
2021-02-14 Lots of changes
    * Dropped LED's and LASER control
    * Renamed DECLINATION to AZIMUTH
    * Moved AZIMUTH control hookup into the globe (it needs to spin freely)
    I couldn't make the LED's fit and shine without casting shadows inside
    the globe. Plus, there wasn't much room, and it required more wires to
    make work. No a critical problem, but the challenges outweighed the
    benefits. I'm going to water color paint the globe now.
    I also removed the LASER control, the manufacturer said don't duty cycle
    it, the built in controls take care of it. This isn't supposed to be on
    constantly anyway.
    [internalhookup.brd, internalhookup.sch, isstracker.brd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]
2021-02-17 PCB fixups
    * Bumped PCB revisions
    * Layout changes and some silk screen updates
    * No functionality changes
    [internalhookup.brd, isstracker.brd, isstracker.sch]
2021-02-23 Fixups
    * Add the ability to turn the power to the globe on and off via a MOSFET
    * Clean up some of the code
    [isstracker.brd, isstracker.sch]
2021-02-23 More fixups
    * Migrate from declination to azimuth
    * Make the globe timeout independent of the display
    [isstracker.ino]
2021-02-24 More fixups
    * Make the globe power control a toggle, the laser may be more robust
    than I assumed
    [isstracker.ino]
2021-02-24 Hookup board revision to 1.6
    * Added a cap in front of the servo as the line to get the 5V is long
    and may not be totally reliable under stress
    [internalhookup.brd, internalhookup.sch]
2021-03-04 Updating to build 53
    * Create a board rev define as I'm testing with an older board. It
    works, but isn't correct
    * Add N/S/E/W to the display to make it more clear where the ISS is
    [isstracker.ino]
2021-03-06 Layout tweaks
    * Swap pth for smd LED's
    * Move globe power pin to new location
    * Add support hole for motor board if attached via headers
    * Layout fixes for globe with new 4 pin setup
    [internalhookup.brd, isstracker.brd, isstracker.sch]
2021-03-06 Control board version 1.7
    * Added a pushbutton to turn the globe back on
    * Began to put globe power control back into app
    [isstracker.brd, isstracker.sch]
2021-03-06 Updating to version 54
    * This cleans up globe power control a lot
    * Adds a lot comments to help undestanding
    * Untested as the unit is still down until I update the boards
2021-03-06 Bump control board revision
    * Move pins around for display, motion, and pushbutton
    * Add pushbutton
    [isstracker.brd, isstracker.sch]
2021-03-06 Update to version 1.9
    * Fix the FET, it wasn't right
    * New FET in the BOM
    * Put FET on low side and add pulldown on gate
    [isstracker.brd, isstracker.sch]
2021-03-06 Adding BOM's
    * New BOM's for tracking components
    [internalhookup.ods, isstracker.ods]
2021-03-06 Updating LED BOM entry
    [isstracker.ods]
2021-03-27 Fixes
    * Add globe power using a MOSFET so the laser can be turned on/off
    * Update both board layouts to accomodate new power scheme
    * Fix some component positions in layout
    * Migrate to screw terminals for power on board
    [isstracker.brd, isstracker.sch]

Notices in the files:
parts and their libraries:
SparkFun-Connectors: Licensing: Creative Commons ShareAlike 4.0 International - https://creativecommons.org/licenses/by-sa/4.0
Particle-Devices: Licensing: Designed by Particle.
